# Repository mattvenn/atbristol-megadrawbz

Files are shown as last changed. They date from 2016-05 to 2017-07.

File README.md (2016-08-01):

# @bristol energy drawing robot

## updates

* [youtube playlist](https://www.youtube.com/playlist?list=PLmcDgdDpcaPiOdnMplbk7o1K5Kpvp_UAL)
* [photos](https://goo.gl/photos/KGhmjEyrZScbemvW7)

## details

### hardware

* [Beagle bone breakout board](hardware/bbbbbb_pcb/)
* [Pen holder](hardware/gondola_pcb/)
* [notes on stepper choice](tests/stepper-choice)

### machinekit/linuxcnc configuration

* Robot is controlled with machinekit running on a beaglebone black.
* Pen holder is controlled via Xbee radio and uses a [custom component] that runs in its own realtime thread.

* [configuration](https://github.com/mattvenn/machinekit-bipod)

### firmware

* [pen holder firmware](firmware/gondola/)

### tests

* [prototypes, tests, proof of concepts](tests)

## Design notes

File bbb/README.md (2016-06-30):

# Install

got latest image from
http://elinux.org/Beagleboard:BeagleBoneBlack_Debian#BBW.2FBBB_.28All_Revs.29_Machinekit

then flashed to sd card like
xzcat bone-debian-7.10-machinekit-armhf-2016-04-10-4gb.img.xz | sudo dd of=/dev/sdb

put into bbb and rebooted
username and password is machinekit

used linuxcnc to choose the CRAMPS config and that starts

install machinekit-dev to compile new hals

# Timings

## probotix example - cometnp_metric.ini
xstep is p9.31 11.2khz

default and max velocity for x axis increased to 1000
xstep is p9.31 43khz, nice and even

tested changing pin from 142 to 931 and worked the same

copied cramps settings and got speed of 95khz, less even

## cramps example - cramps.hal

xstep is p8.13 60khz

# Bipod setup

comp --install wanted a posix directory. Made and then copied over. Warning
about sqrt.

Can't start linuxcnc, got a permission error similar to stuarts.

to do with missing vtable in bipodkins. Clues from
https://groups.google.com/forum/#!searchin/machinekit/vtable$20kinematics/machinekit/qNgl9Eb5cbA/jJzNCTshsm0J

took code from
https://github.com/machinekit/machinekit/pull/560/commits/9b60f6636091e8badb550a7804e23cf311424cd2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

kins needs to be specified with motmod or will default to trivkins.

joint following errors were fixed (I think) by adding a maximum_acceleration in
the `[traj]` section.

# Serial setup

    # doesn't play well with the setup.sh that machinekit config uses
    echo BB-UART1 > /sys/devices/bone_capemgr.*/slots
    dmesg | grep tty

check connected xbee

    miniterm.py /dev/ttyO1 57600
    +++

replies with `OK`.

## path

add this to ~/.bashrc:

    PATH=$PATH:/home/machinekit/machinekit/configs/machinekit-bipod

not needed as can do loadusr ./xbee.py
loadusr needs -W parameter to wait till it initialises, probably why it was
occasionally failing on pc.

# startup issues

    Machine configuration directory is
    '/home/machinekit/machinekit/configs/machinekit-bipod'
    Machine configuration file is 'bipod.ini'
    Starting Machinekit...
    io started
    emc/iotask/ioControl.cc 752: can't load tool table.
    halcmd loadusr io started
    Loading cape-universal overlay to /sys/devices/bone_capemgr.9/slots
    X11 connection rejected because of wrong authentication.
    PRU control files not found in /sys/class/uio/uio0
    bipod.hal:10: program './setup.sh' failed, returned 1
    Shutting down and cleaning up Machinekit...

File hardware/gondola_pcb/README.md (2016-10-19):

# gondola PCB

## mods made

* connect xbee rx & tx to atmel rx & tx (no software serial) - solder wires to xbee header and connected a header that plugs into the programming header
* [lipo charger](http://dlnmh9ip6v2uc.cloudfront.net/datasheets/Prototyping/TP4056.pdf) soldered to the back, connected pin 7 to charge pin on pcb

## fixes required for next version

* lipo charger on board
* reset button
* reset xbee from atmega
* remote firmware update - arduino needs to reset itself 
* lipo socket that fits
* crystal footprint, no load caps required!
* lower frequency crtstal, mega328 is only guaranteed to 10mhz on 3.3v

## xbee firmware update

* has to be hw. tried sw and didn't work. used a 2n3904 to invert the signal and pull reset low
* haven't tried with xbee yet.
* wide timing window : 900ms before or after avrdude is run

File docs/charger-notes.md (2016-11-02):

# Tue Oct 18 14:46:19 CEST 2016

old charger (tp4506) and new (mcp73831) both can get stuck if the battery gets too low.
seems to be because xbee is drawing too much current so battery doesn't see enough

with xbee connected charge current is 0ma
with xbee disconnected is 10ma

current drawn on circuit is 50ma without xbee, 100 with. Why so high without?
should be about 6ma.

could be worth looking at xbee sleep modes before hacking on power control
(need to do ATSM1 to enable pin)

could also put a mosfet on the charger board that will not connect main board until vbatt > thresh

thoughts:
* 500ma maybe too high a charge current
* make sure charge sense pin can't do damage to atmega

charge sense pin on broken pcb seems shorted to ground, need to check the
old charger pcb

# Wed Oct 19 15:21:23 CEST 2016

why did charge pin get damaged?

* input higher than supply voltage?

charge sense pin was (I think - should have taken a photo before disconnecting)
connected to other side of diode. This voltage is then the diode drop over the
diode subtracted from the supply (which I think I cranked to about 5.5v - again
don't have a record). So about 3.6->4v. And the supply of the chip was 3.3v so
that was probably it.

The same will happen with the mcp73831 as the stat pin goes high when charge is
finished, the high level is vdd-1 so 4v.

# Wed Oct 19 17:39:25 CEST 2016

* questions - why current draw so high?
* why won't battery charger to higher than 3.8?

battery doc is 
http://es.rs-online.com/webdocs/141b/0900766b8141bf6b.pdf

# Thu Oct 27 18:51:30 CEST 2016

* discharged at 400ma till cutoff
* testing with 171ma current limit with battery fully discharged (v drops to
 3.7v)

start, gondola comes on, but has problems with comms:

inekit@devel:~/bipod$ halcmd  show | grep xbee
    94  User          0 xbee                                      18964 ready, u1:0 u2:0
    94        u32   OUT    0x00001AA8  xbee.cksum-err 0
    94        float OUT          0.26  xbee.gond_batt                   0.000010 0
    94        u32   OUT    0x0000AA6B  xbee.gond_err_count 0
    94        u32   OUT    0x00000000  xbee.gond_flags 0
    94        u32   OUT    0x00000000  xbee.gond_rx_count 0
    94        u32   OUT    0x00000000  xbee.gond_touch 0
    94        float IN              8  xbee.pos                         0.000010 0 <== zpos
    94        u32   OUT    0x0001280B  xbee.rx-err 0
    94        bit   IN           TRUE  xbee.servo_enable 0 ==> xbee.pos
    94        float RW             20  xbee.scale

comms problem fixed with start byte.

Also changed to 300mA charge current

# Wed Nov  2 09:22:05 CET 2016

[low-power-test.sh](low-power-test.sh) used to test what happens with constant
discharge and recharge at the cutoff point. 
[Results show no problems](low-power.log)

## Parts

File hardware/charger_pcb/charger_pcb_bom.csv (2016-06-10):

Qty | Value | Device | Package | Parts | Description | RS code | Link
2 |  | AK500/2 | AK500/2 | X1, X2 | CONNECTOR | 2204260 | http://uk.rs-online.com/web/p/pcb-terminal-blocks/2204260/
1 |  | LEDCHIP-LED0805 | CHIP-LED0805 | POWER | LED | 8886057 | http://uk.rs-online.com/web/p/visible-leds/9154768/
2 |  | N-MOSFET-SO8S | SO-08 | Q1, Q2 | N-Channel MOSFET | 915-4960 | http://uk.rs-online.com/web/p/mosfet-transistors/9154960/
1 | 0.01uF | C-EUC0805 | C0805 | C2 | CAPACITOR, European symbol | 4614013 | http://uk.rs-online.com/web/p/ceramic-multilayer-capacitors/4614013/
1 | 0.01uf | C-EUC0805 | C0805 | C1 | CAPACITOR, European symbol | 4614013 | http://uk.rs-online.com/web/p/ceramic-multilayer-capacitors/4614013/
1 | 0.3uF | C-EUC0805 | C0805 | C3 | CAPACITOR, European symbol | 6983421 | http://uk.rs-online.com/web/p/ceramic-multilayer-capacitors/6983421/
2 | 100R | R-EU_R0805 | R0805 | R1, R2 | RESISTOR, European symbol | 6790807 | http://uk.rs-online.com/web/p/surface-mount-fixed-resistors/6790807/
1 | 16VZ | ZENER-DIODESOD80C | SOD80C | D2 | Z-Diode | 7598775 | http://uk.rs-online.com/web/p/zener-diodes/7598775/
1 | 16vZ | ZENER-DIODESOD80C | SOD80C | D1 | Z-Diode | 7598775 | http://uk.rs-online.com/web/p/zener-diodes/7598775/
1 | 220R | R-EU_R0805 | R0805 | R3 | RESISTOR, European symbol | 2230332 | http://uk.rs-online.com/web/p/surface-mount-fixed-resistors/2230332/
2 | 40V2A | MBRA340T3 | SMA | D3, D4 | Surface Mount Schottky Power Rectifier | 708-2337 | http://uk.rs-online.com/web/p/rectifier-schottky-diodes/7082337/
2 | 68uH | L-EUL5650M | L5650M | L1, L2 | INDUCTOR, European symbol | 6924930 | http://uk.rs-online.com/web/p/wire-wound-surface-mount-inductors/6924930/

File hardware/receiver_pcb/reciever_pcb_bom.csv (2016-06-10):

Part | Value | Device | Package | Description | RS code | Link
C1 | 4.7nF | C-EUC0805 | C0805 | CAPACITOR, European symbol | 4646717 | http://uk.rs-online.com/web/p/ceramic-multilayer-capacitors/4646717/
C2 | 4.7nF | C-EUC0805 | C0805 | CAPACITOR, European symbol | 4646717 | http://uk.rs-online.com/web/p/ceramic-multilayer-capacitors/4646717/
C3 | 22nF | C-EUC0805 | C0805 | CAPACITOR, European symbol | 4646701 | http://uk.rs-online.com/web/p/ceramic-multilayer-capacitors/4646701/
C4 | 1.8nF | C-EUC0805 | C0805 | CAPACITOR, European symbol | 7236225 | http://uk.rs-online.com/web/p/ceramic-multilayer-capacitors/7236225/ | Low ESR
C5 | 10uF | C-EUC0805 | C0805 | CAPACITOR, European symbol | 9159280 | http://uk.rs-online.com/web/p/ceramic-multilayer-capacitors/9159280/ | Low ESR
C6 | 2.2uF | C-EUC0805 | C0805 | CAPACITOR, European symbol | 8919794 | http://uk.rs-online.com/web/p/ceramic-multilayer-capacitors/8919794/
C7 | 10nF | C-EUC0805 | C0805 | CAPACITOR, European symbol | 4614013 | http://uk.rs-online.com/web/p/ceramic-multilayer-capacitors/4614013/
D1 | DFLS240L | DFLS240L | POWERDI123 |  | 7082337 | http://uk.rs-online.com/web/p/rectifier-schottky-diodes/7082337/ | Ordered 10 on charger, 10 on reciever
D2 | DFLS240L | DFLS240L | POWERDI123 |  | 7082337 | http://uk.rs-online.com/web/p/rectifier-schottky-diodes/7082337/
D3 | DFLS240L | DFLS240L | POWERDI123 |  | 7082337 | http://uk.rs-online.com/web/p/rectifier-schottky-diodes/7082337/
D4 | 39VZ | DFLZ39 | POWERDI123 |  | 822-2497 | http://uk.rs-online.com/web/p/zener-diodes/8222497/
L1 | 15uH | L-EUL1812 | L1812 | Toko coil | 7521327 | http://uk.rs-online.com/web/p/wire-wound-surface-mount-inductors/7521327/ | out of stock, using this: http://uk.rs-online.com/web/p/wire-wound-surface-mount-inductors/0573858/
LED1 |  | LEDCHIP-LED0805 | CHIP-LED0805 | LED |  | http://uk.rs-online.com/web/p/visible-leds/9154768/ | ordered on charger
LED2 |  | LEDCHIP-LED0805 | CHIP-LED0805 | LED |  | http://uk.rs-online.com/web/p/visible-leds/9154768/
R1 | 3.01K | R-EU_R0805 | R0805 | RESISTOR, European symbol | 6791349 | http://uk.rs-online.com/web/p/surface-mount-fixed-resistors/6791349/
R2 | 10K | R-EU_R0805 | R0805 | RESISTOR, European symbol | 2230562 | http://uk.rs-online.com/web/p/surface-mount-fixed-resistors/2230562/
R3 | 22k | Pot |  | Charge limiting pot | 5219754 | http://uk.rs-online.com/web/p/trimmer-resistors/5219754/
R4 | 470 | R-EU_R0805 | R0805 | RESISTOR, European symbol | 2230376 | http://uk.rs-online.com/web/p/surface-mount-fixed-resistors/2230376/
R5 | 470 | R-EU_R0805 | R0805 | RESISTOR, European symbol | 2230376 | http://uk.rs-online.com/web/p/surface-mount-fixed-resistors/2230376/
U$1 | LT4120 | LT4120 | QFN16 |  |  |  | Matt has them, for free!
X1 |  | AK500/2 | AK500/2 | CONNECTOR |  | http://uk.rs-online.com/web/p/pcb-terminal-blocks/2204260/ | ordered on charger
X2 |  | AK500/2 | AK500/2 | CONNECTOR |  | http://uk.rs-online.com/web/p/pcb-terminal-blocks/2204260/ | ordered on charger
X3 |  | KK-156-3 | KK-156-3 | KK 156 HEADER |  |  | Matt has them, and also a crimper
X4 |  | AK500/2 | AK500/2 | CONNECTOR | 5151383 | http://uk.rs-online.com/web/p/pcb-headers/5151383/ | Jst battery connector
 | 2000mA/h |  |  | Lipo | 7916460 | http://uk.rs-online.com/web/p/lithium-rechargeable-battery-packs/7916460/

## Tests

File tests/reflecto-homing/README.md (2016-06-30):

# Testing reflective homing

This method of homing is interesting to explore because it means our home point can be in the middle of the robot's range rather than at the edges. The edges are harder to get to because if the motors aren't co-ordinated (like at power on) there can be too much tension in the strings.

It's also interesting because if we can sense the string on the spool we have a 1 bit absolute position sensor. This means even if this method can't provide precision homing, it will help move the motors to a safe starting place before a more traditional homing method is used.

Test shows the homing is accurate to within +- 0.15mm (on a 19mm spool). However, the results are susceptible to changes in ambient light. With a torch I can produce a 0.5mm error.

## Setup

[Video](https://www.youtube.com/watch?v=r71VegIOap8&feature=youtu.be)

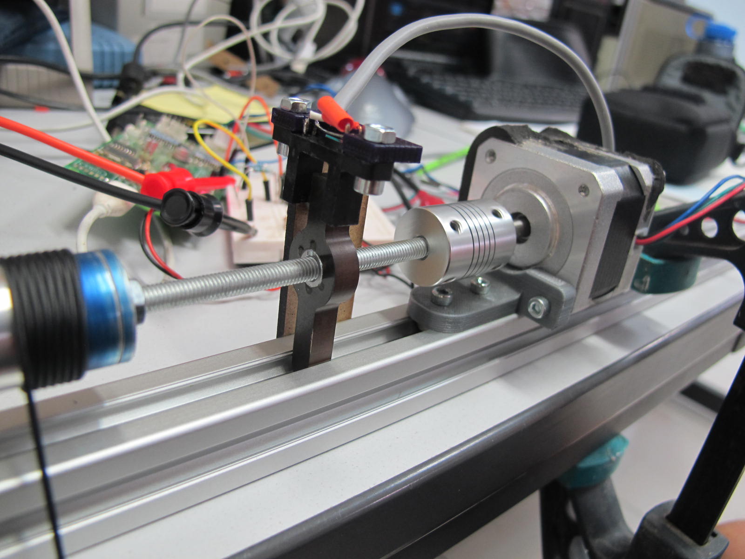
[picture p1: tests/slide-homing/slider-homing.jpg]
setup


* 1600 count encoder with thread wrapped twice
* 8 time microstepping
* 12v
* 0.2A
* 130g weight
* using [OPB608A](http://uk.rs-online.com/web/p/photoelectric-sensors/1944018/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)

## Results

* spool is black nylon with a 1mm thread, string is generic brown braid, about 0.8mm

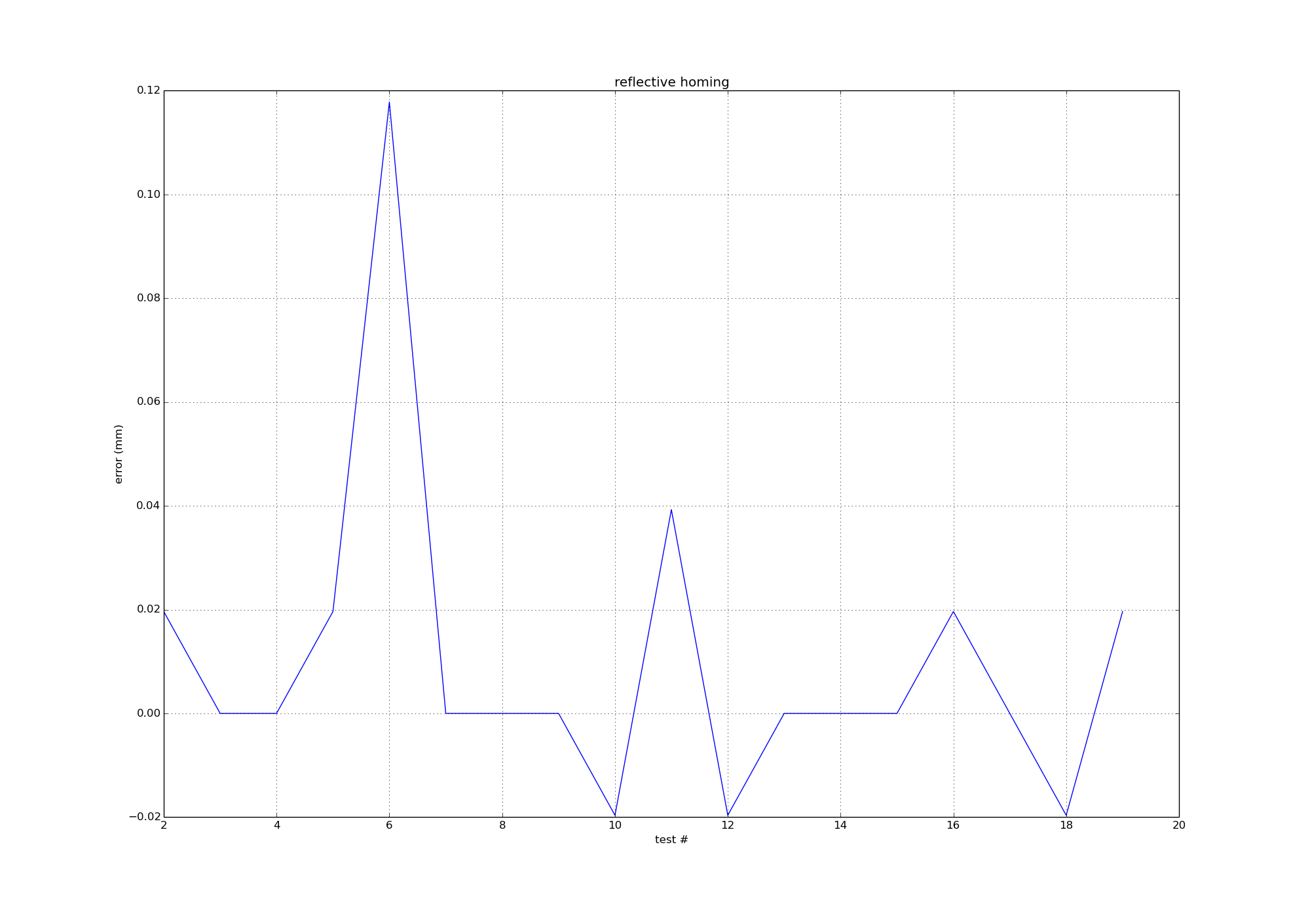
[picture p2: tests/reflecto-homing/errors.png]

[data](home_errors.pkl)

* black 1mm dyneema on aluminium spool, 10k R on opto collector

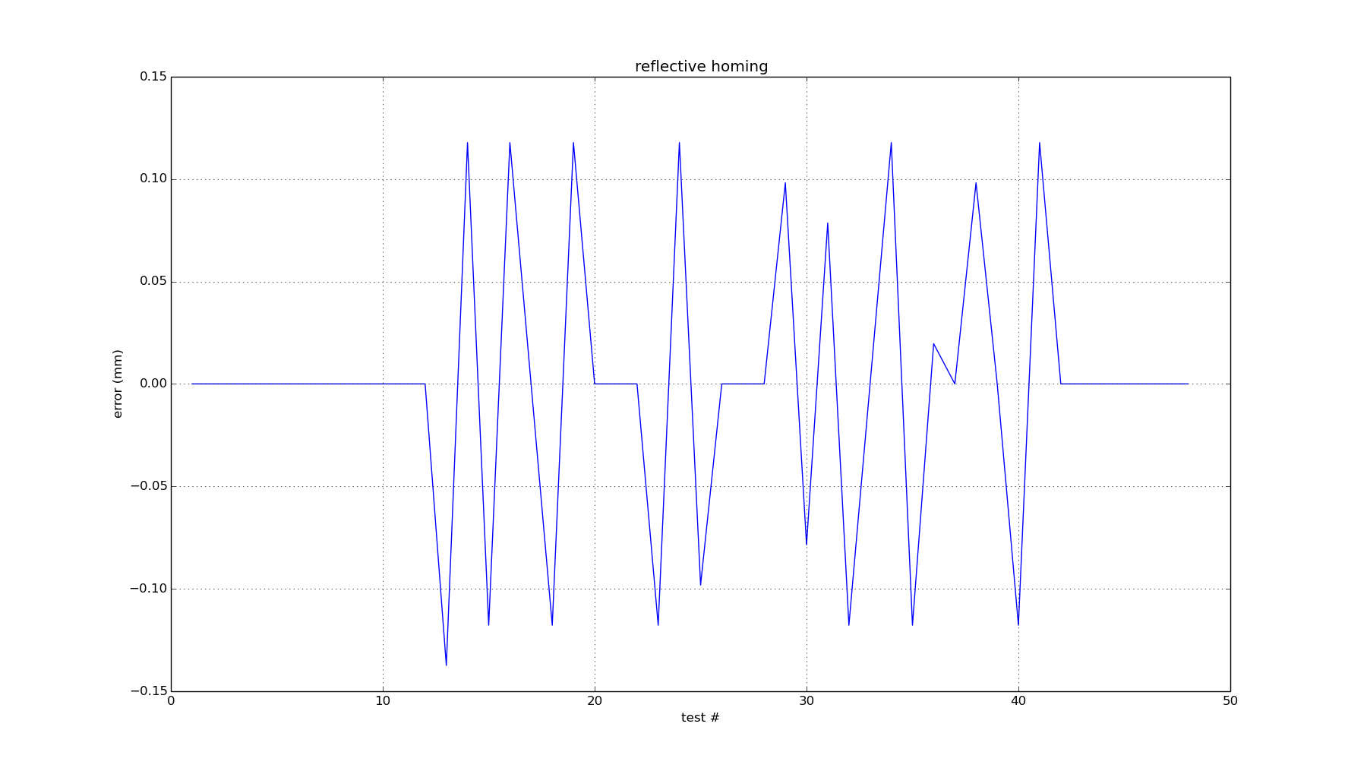
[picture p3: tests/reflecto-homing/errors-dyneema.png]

[data](home_errors-dyneema.pkl)

* black 1mm dyneema on aluminium spool, screwthread 1.3mm

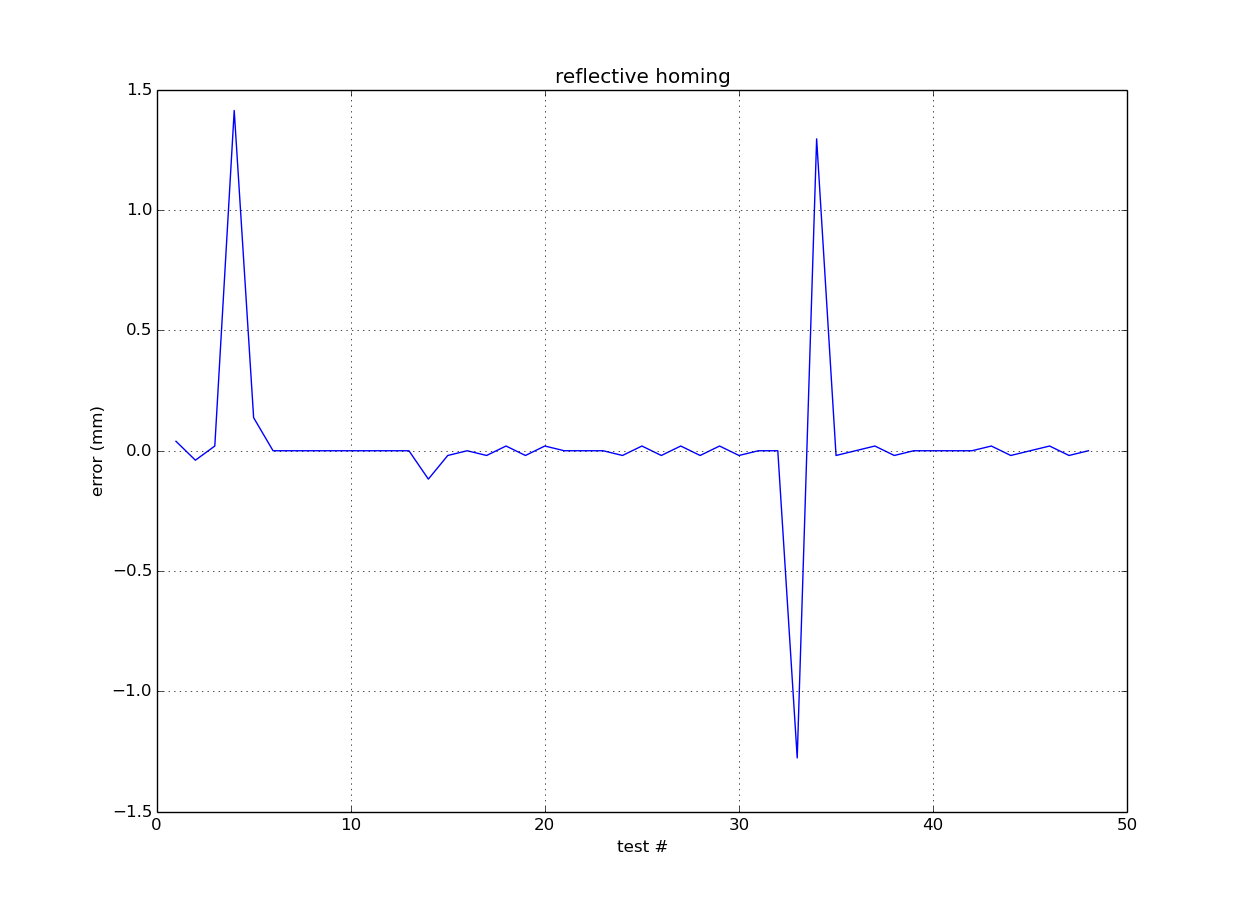
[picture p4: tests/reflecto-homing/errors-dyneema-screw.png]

[data](home_errors-dyneema-screwthread.pkl)

* 20uf cap on opto supply and 100nf on opto output, slowed home speed

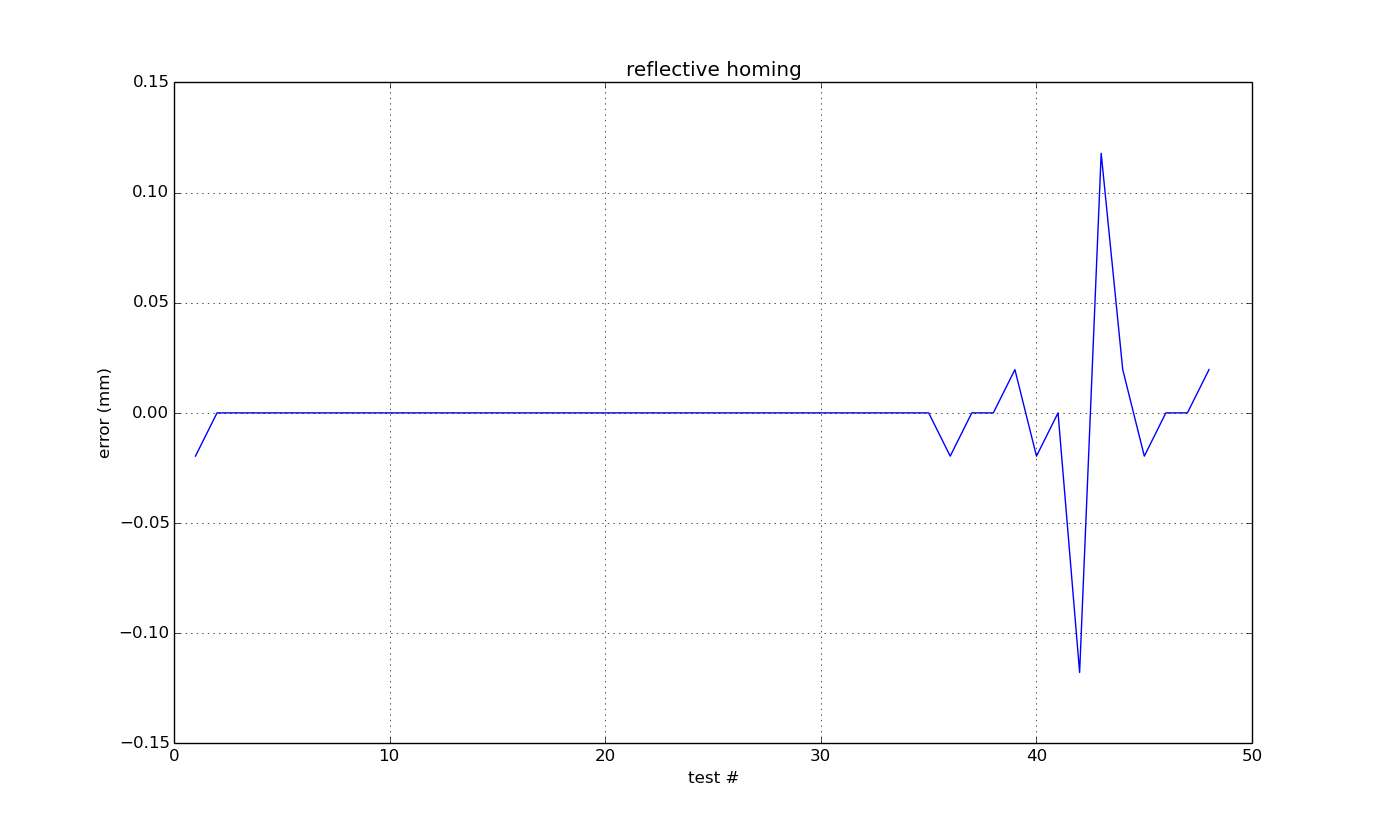
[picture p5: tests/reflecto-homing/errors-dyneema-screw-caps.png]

[data](home_errors-dyneema-screwthread-caps.pkl)

* same as last test but sensor rotated 90

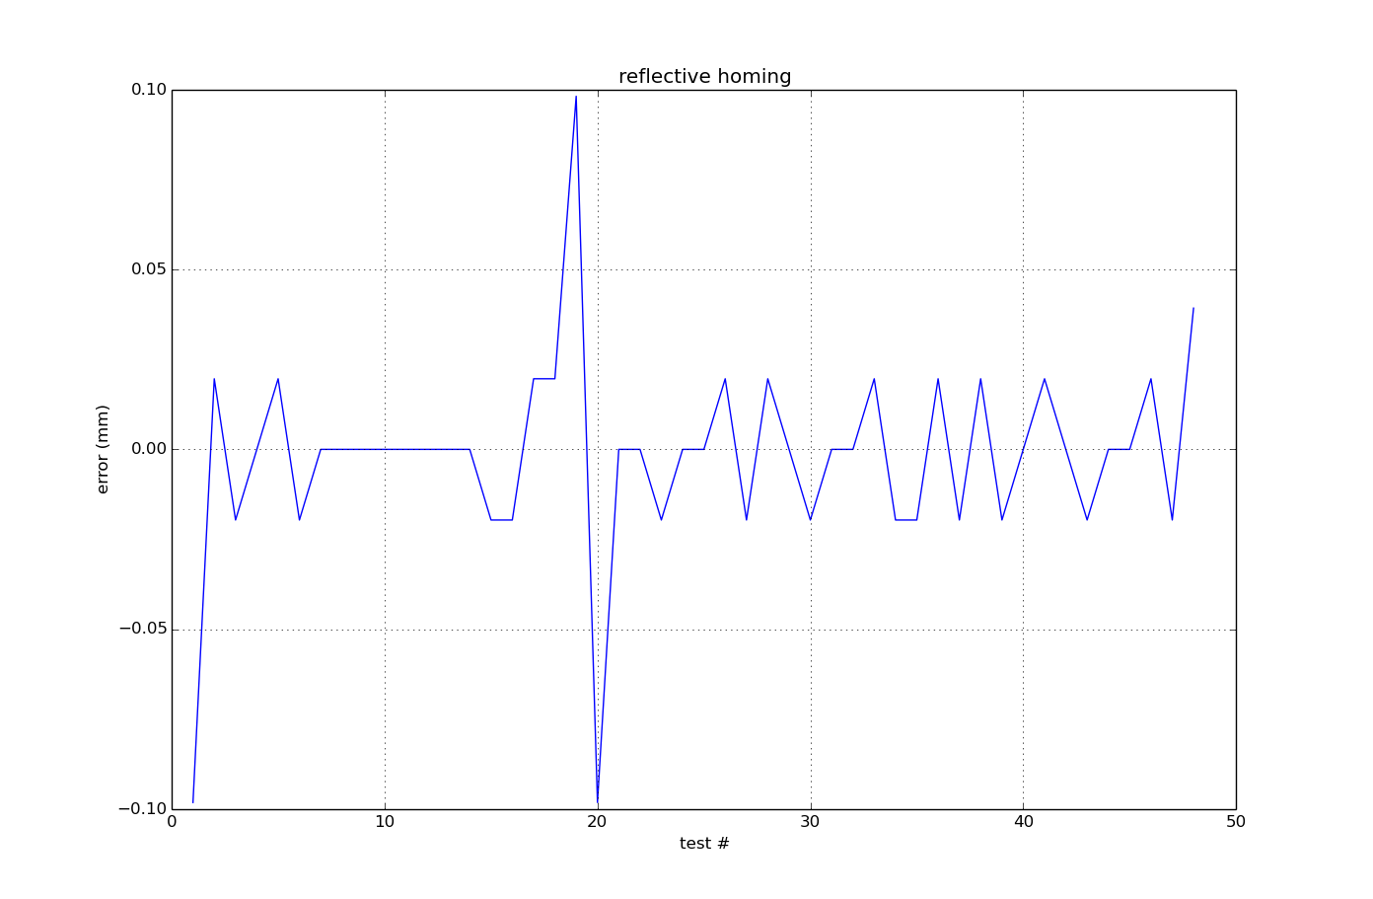
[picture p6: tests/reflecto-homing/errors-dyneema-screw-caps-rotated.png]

[data](home_errors-dyneema-screwthread-caps-rotated.pkl)

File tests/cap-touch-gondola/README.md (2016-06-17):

# capacitive touch on the gondola

If people lift the gondola the strings can unwind or get tangled

We're planning on using PTFE tube for the string to run through at the top corners, which will stop the lack of tension getting through to the spools.

However if the gondola is lifted if the spools are unwinding the string could get tangled up.

So this test is to see if the gondola can sense when it's touched, and send a signal to linuxcnc to pause the drawing.

We were worried that without a ground connection the capacitive touch method wouldn't work, but it seems to work fine.

# method

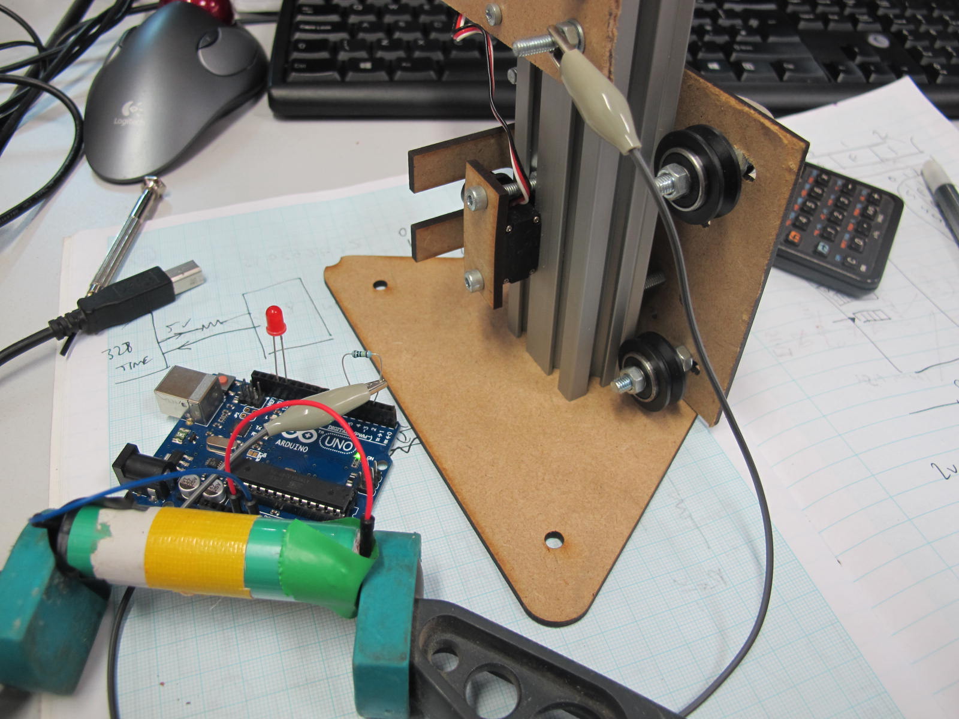
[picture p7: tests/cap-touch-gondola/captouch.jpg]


[video](https://www.youtube.com/watch?v=7M-Ta0E2XPM&feature=youtu.be)

a 1M resistor is connected between 2 pins. One of the pins is also connected to the aluminium of the gondola.

# test code

[cap.ino](cap.ino)

using this [capacitive touch library](https://github.com/PaulStoffregen/CapacitiveSensor)

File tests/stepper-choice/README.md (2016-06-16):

# Stepper choice

specs:

* 1Nm to provide resistance against tampering
* string on a 35mm spool to reduce wrapping (and therefore hyp error)
* hyp error <= 0.2mm over travel
* max spd >= 150mm/s
* res <= 0.2 mm/step

# chosen option:

* motor: http://uk.rs-online.com/web/p/stepper-motors/5350423/
* 1nm at 2.8A, 200 steps per rev
* 1 : 1.8 pulley ratio

[datasheet](http://docs-europe.electrocomponents.com/webdocs/07e2/0900766b807e2898.pdf)

We should be able to achieve 1nm with about half the rated current but if
necessary we can increase the current. We also have options to increase torque
by decreasing microstepping at the cost resolution.

At 2000hz step freq, we achieve 150mm/s and datasheet says torque is derated by
20%.

## option 1

http://uk.rs-online.com/web/p/stepper-motors/5350502/
400 steps/rev, 1.26nm, 2.8A

config: micro steps is 2, and motor is directly attached

20% overrated so can run at 2.2A
cost = £35

## option 2

http://uk.rs-online.com/web/p/stepper-motors/5350401/?origin=null|fp&cm_sp=featureproducts-_-FeaturedProductsContent-_-5350401

200 steps/rev
0.44Nm, 1.68A

config: micro steps is 2, motor is attached with 1:2 pulley

cost = £27 + pulleys & belts (£11 + £3)
total = £40

notes: slightly underrated

## option 3

http://uk.rs-online.com/web/p/stepper-motors/5350445/
1.89Nm 2.8A

directly attached with 4 x microstepping
cost = £41.20

notes: 2.8A is above the drivers can supply

# Driver

## drv8825

rds on at 85C = 0.32R
page 23 data sheet:

    Ptot = 4*rdson*(iout)^2
    = 6W dissipation

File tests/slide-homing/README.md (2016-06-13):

# Testing sliding homing

The [reflective homing
method](https://github.com/mattvenn/atbristol-megadrawbz/tree/master/tests/reflecto-homing) had some good benefits, but suffered from unreliability
with changing light conditions. In particular we wanted to keep the absolute
positioning to aid with homing. Ideally we want the method to be good enough for
homing (better than 0.3mm error).

For this test we coupled the spool with a screwthread and used the thread to
drive a slider that interrupted the photo interrupter.

Results show better than opto homing (0.12mm max error on a 19mm spool), and
much more reliable. With a bit more tuning we should get even lower errors, but
our calculations show that 0.3mm error is acceptable.

## Setup

setup

[Video here](https://www.youtube.com/watch?v=r71VegIOap8&feature=youtu.be)

* 8 time microstepping
* 12v
* 0.2A
* m6 threaded bar, rexroth extrusion for rail
* direct drive stepper
* 10k R on opto collector [Optek OPB815L](http://uk.rs-online.com/web/p/slotted-optical-switches/1944024/)
* 35mm diameter spool

## Results

All plots show errors in mm calculated for a 35mm diameter spool.

* 2000 steps and with a short backoff. 

[data](error-2000step.pkl) 
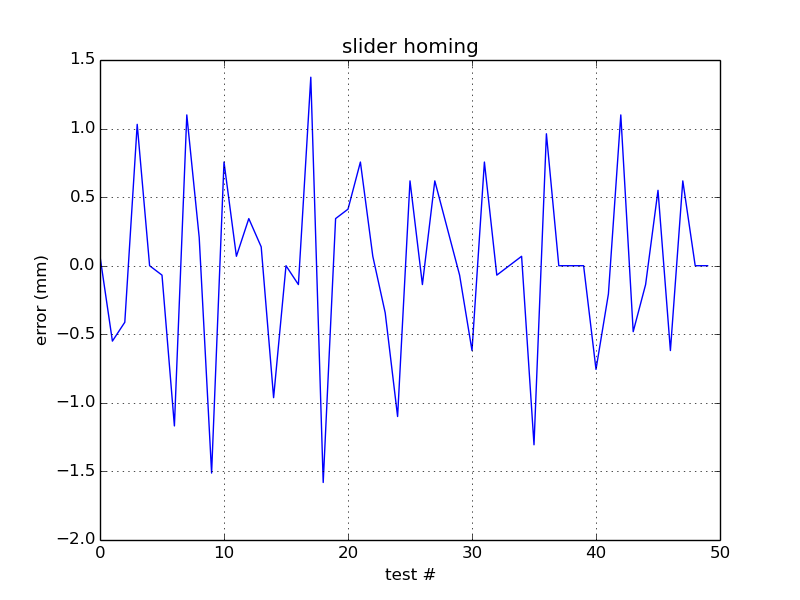
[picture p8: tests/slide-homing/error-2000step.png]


* tufnol slider, pressfit nut, 4000 step

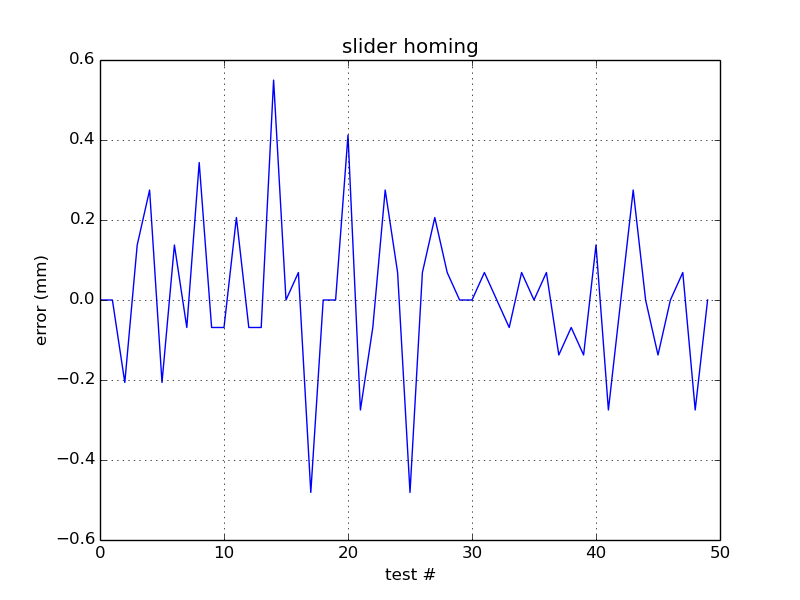
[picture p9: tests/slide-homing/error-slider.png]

[data](error-slider.pkl)

The slider was doing some wobbling, tried with a spring but made it worse.

* 3d printed slider with 2 press fit nuts

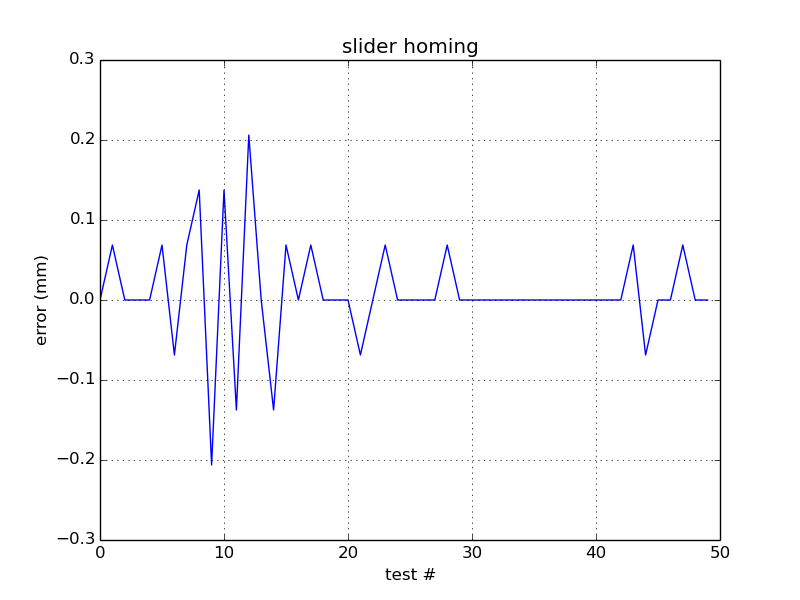
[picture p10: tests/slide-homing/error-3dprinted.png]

[data](error-3dprinted.pkl)

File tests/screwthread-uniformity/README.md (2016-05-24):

# Testing screw thread uniformity

setup



* standard M10 threaded bar mounted to NEMA17 200 steps per rev stepper
* 8 time microstepping
* 12v
* 0.2A
* 130g weight

[Test program](test.py) sends steps for 10 revolutions, recording encoder position at each 20 step interval.

[firmware](screwthread-uniformity.ino) is running on Arduino.

# Results

Graphs generated by [plot.py](plot.py)

* Green line is 1 to 1 stepper to encoder (perfect linearity)
* Blue line is measured stepper vs encoder

## 300 mm

300mm between enc and step

Graph shows excellent linearity between steps and string length

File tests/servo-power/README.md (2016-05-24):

# Battery servo test

## mini servo measurements

* using 10R resister to measure current on scope. 
* Movement from 0 to 100 degrees takes 300ms
* Multimeter shows peak 180mA, avg seems about 30mA
* Integrated curve with scope and got 90mvS, divide by 10R to get 9mAS

* movements each use 9mAS = 0.0025mAH. So to consume 500mAH is 200k moves
* 2k moves use 5mAH

To do a proper test need to move servo more frequently and use a much lower capacity battery.

## Test spec

arduino powered by laptop, servo powered by battery
battery is Panasonic NCR 18650 A Li-Ion 3100mAh 3.7V - [discharge curve](http://2.bp.blogspot.com/-QMeGi0AFhtQ/T2ztWwjDEEI/AAAAAAAADOk/ZcpiqvsJT-g/s1600/Panasonic+3100mAh.jpg)
1 movement every second
4.20V battery at Thu May 19 11:50:19 CEST 2016

2k movements in 2k s = 33min. Test stopped at 12:23. Battery voltage = 4.17V
Additional 2k moves goes to 4.15V
predicted 4v

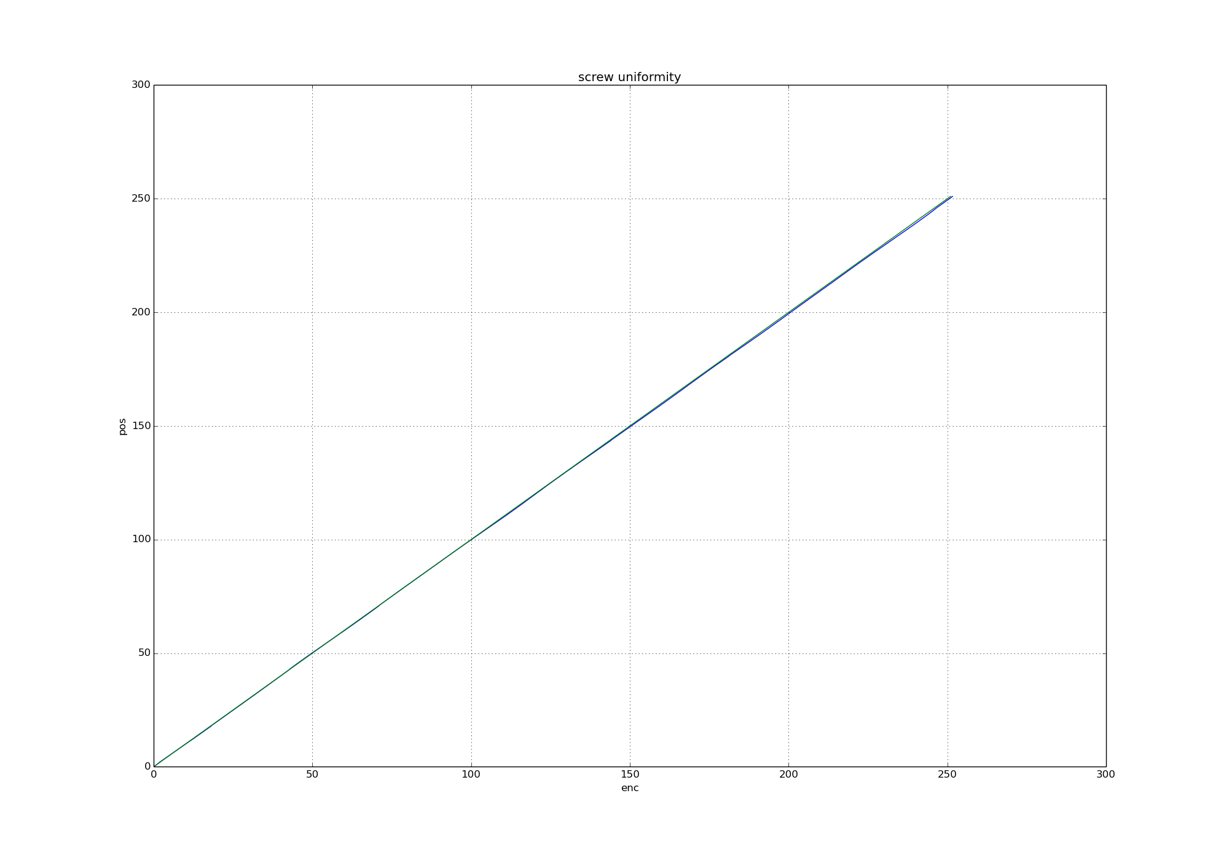
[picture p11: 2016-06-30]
tests/screwthread-uniformity/figure_30-dyneema.png

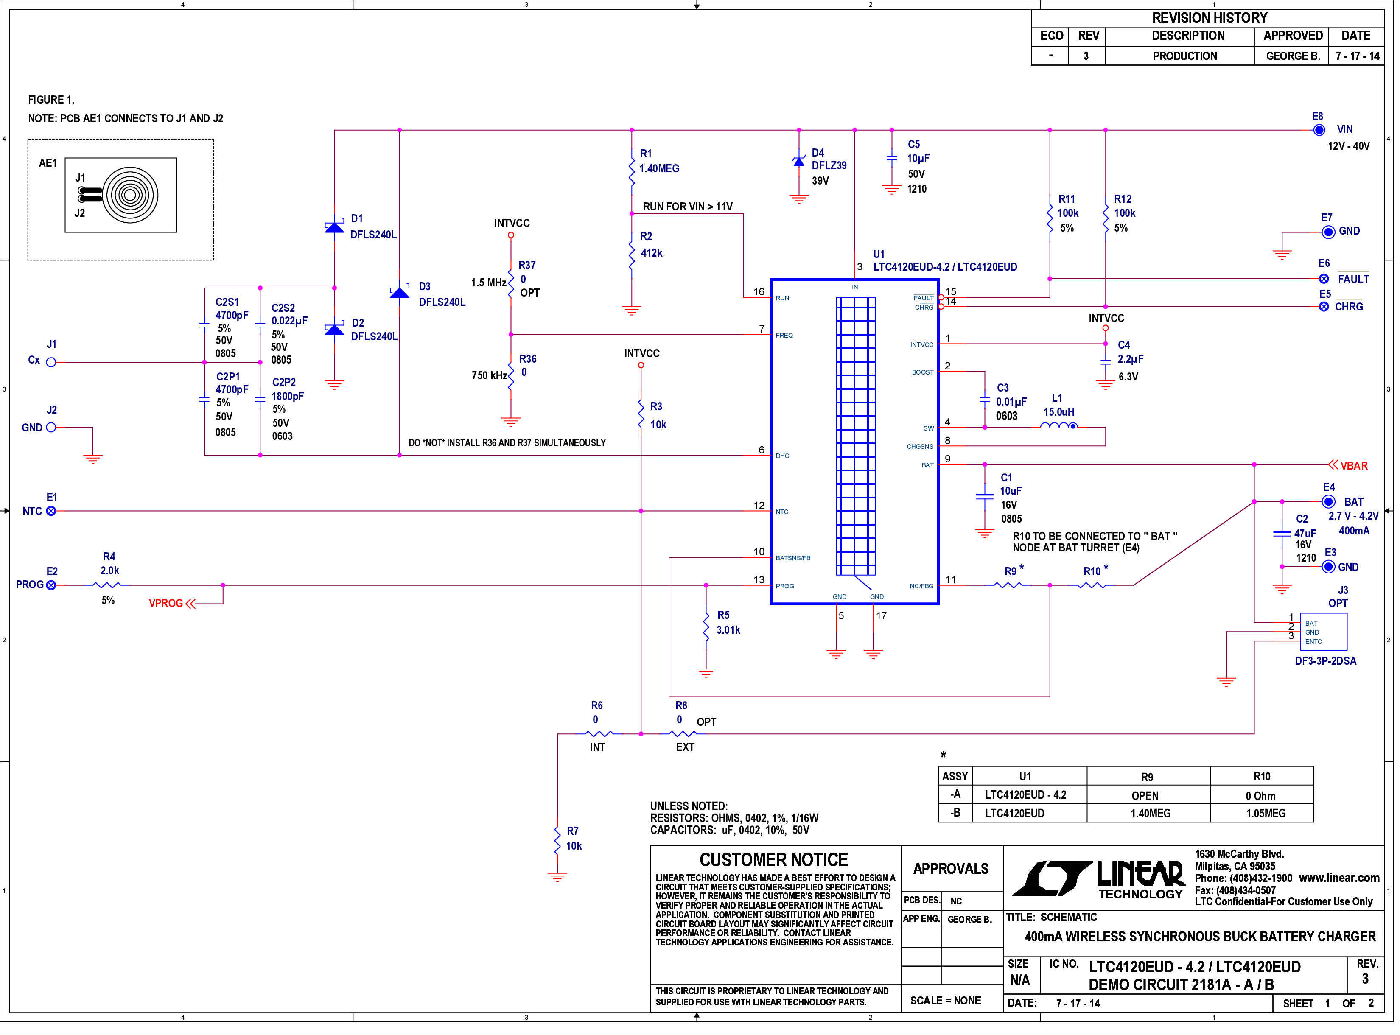
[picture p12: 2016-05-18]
hardware/receiver_pcb/linear test pcb schematic.png

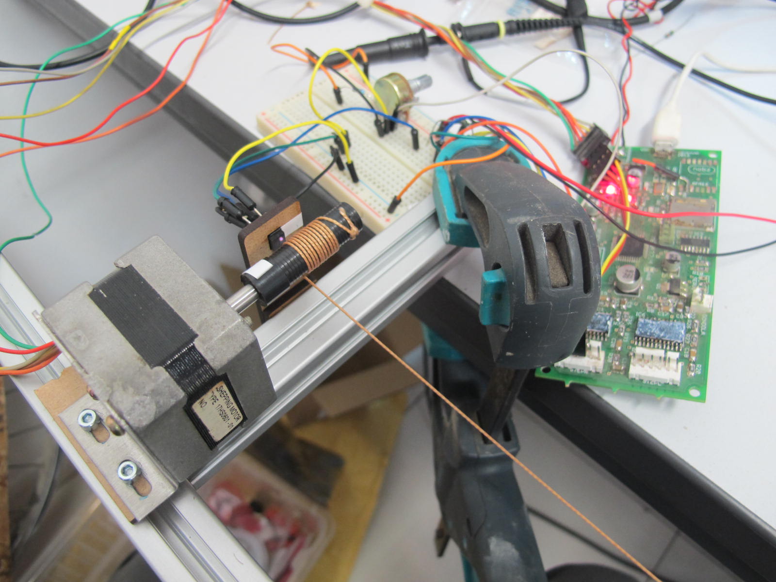
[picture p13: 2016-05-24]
tests/reflecto-homing/ref_homing.jpg

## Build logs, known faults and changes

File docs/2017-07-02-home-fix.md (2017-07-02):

Reset home position

* measured from pulleys and changed in bipod.ini, was 25mm diff on both sides
* was bottoming out at bottom of the circle, so reduced top margin
* changed top margin from 600 to 500 in the cursivedata db on mattvenn.net
* roll fitted wrong way round, so ratchet isn't working

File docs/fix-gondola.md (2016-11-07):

# Gondola fix

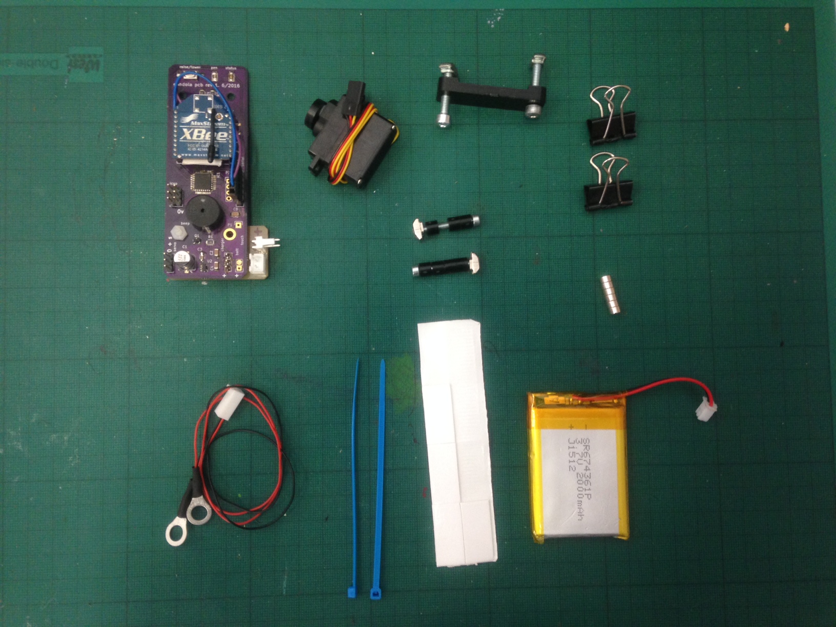
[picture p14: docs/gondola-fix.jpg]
gondola fix kit


## tools required

* 2.5mm hex
* 3mm hex
* small cross head screwdriver
* 8mm spanner
* ladder

## work required

### install servo

* cam angle will need adjusting before fitting
* use cable tie to shorten excess cable

### install battery

* use sticky pads to hold in place, check PCB position first

### install pcb

* use 1 spacer above and 2 below at one end, and 1 above and 3 below for the other
* plug in battery (polarised plug)
* plug in servo (non polarised plug so note polarity on pcb - black is 0v)

### install charger cable

* check polarity of charger hangers before attaching wires to the bolts
* plug in charger cable (polarised plug)

### adjust pen set tool

* after servo change will need to adjust pen test

### improve charger connection

* clean conductive grease
* try out magnets, hold in place with clips
* put conductive grease on charging hangers

# String untangle

## tools required

* 5mm hex key for bolts

## work required

* untangle string
* check homing works correctly

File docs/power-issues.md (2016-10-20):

# Thu Oct 20 11:45:22 CEST 2016

trying to track down spurious power downs:

tried with a brand new beagleboard and this happened within 5 mins!

on terminal:

    Broadcast message from root@devel (Sun Apr 10 20:26:04 2016):

    Power button pressed 
    The system is going down for system halt NOW!

http://bugs.elinux.org/issues/85

trying this:
http://unix.stackexchange.com/questions/114535/system-is-going-down-for-reboot-now

and got this:

    root       575     1  0 11:41 ?        00:00:00 /usr/sbin/acpid
    root     11680   575  0 13:10 ?        00:00:00  \_ /bin/sh -c
    /etc/acpi/powerbtn-acpi-support.sh
    root     11681 11680  0 13:10 ?        00:00:00      \_ /bin/sh
    /etc/acpi/powerbtn-acpi-support.sh
    root     11721 11681  0 13:10 ?        00:00:00          \_ /bin/bash
    /sbin/shutdown -h -P now Power button pressed
    root     11723 11721  0 13:10 ?        00:00:00              \_ ps -ef --forest

So it's a bug in the hardware or software, but easy to fix.

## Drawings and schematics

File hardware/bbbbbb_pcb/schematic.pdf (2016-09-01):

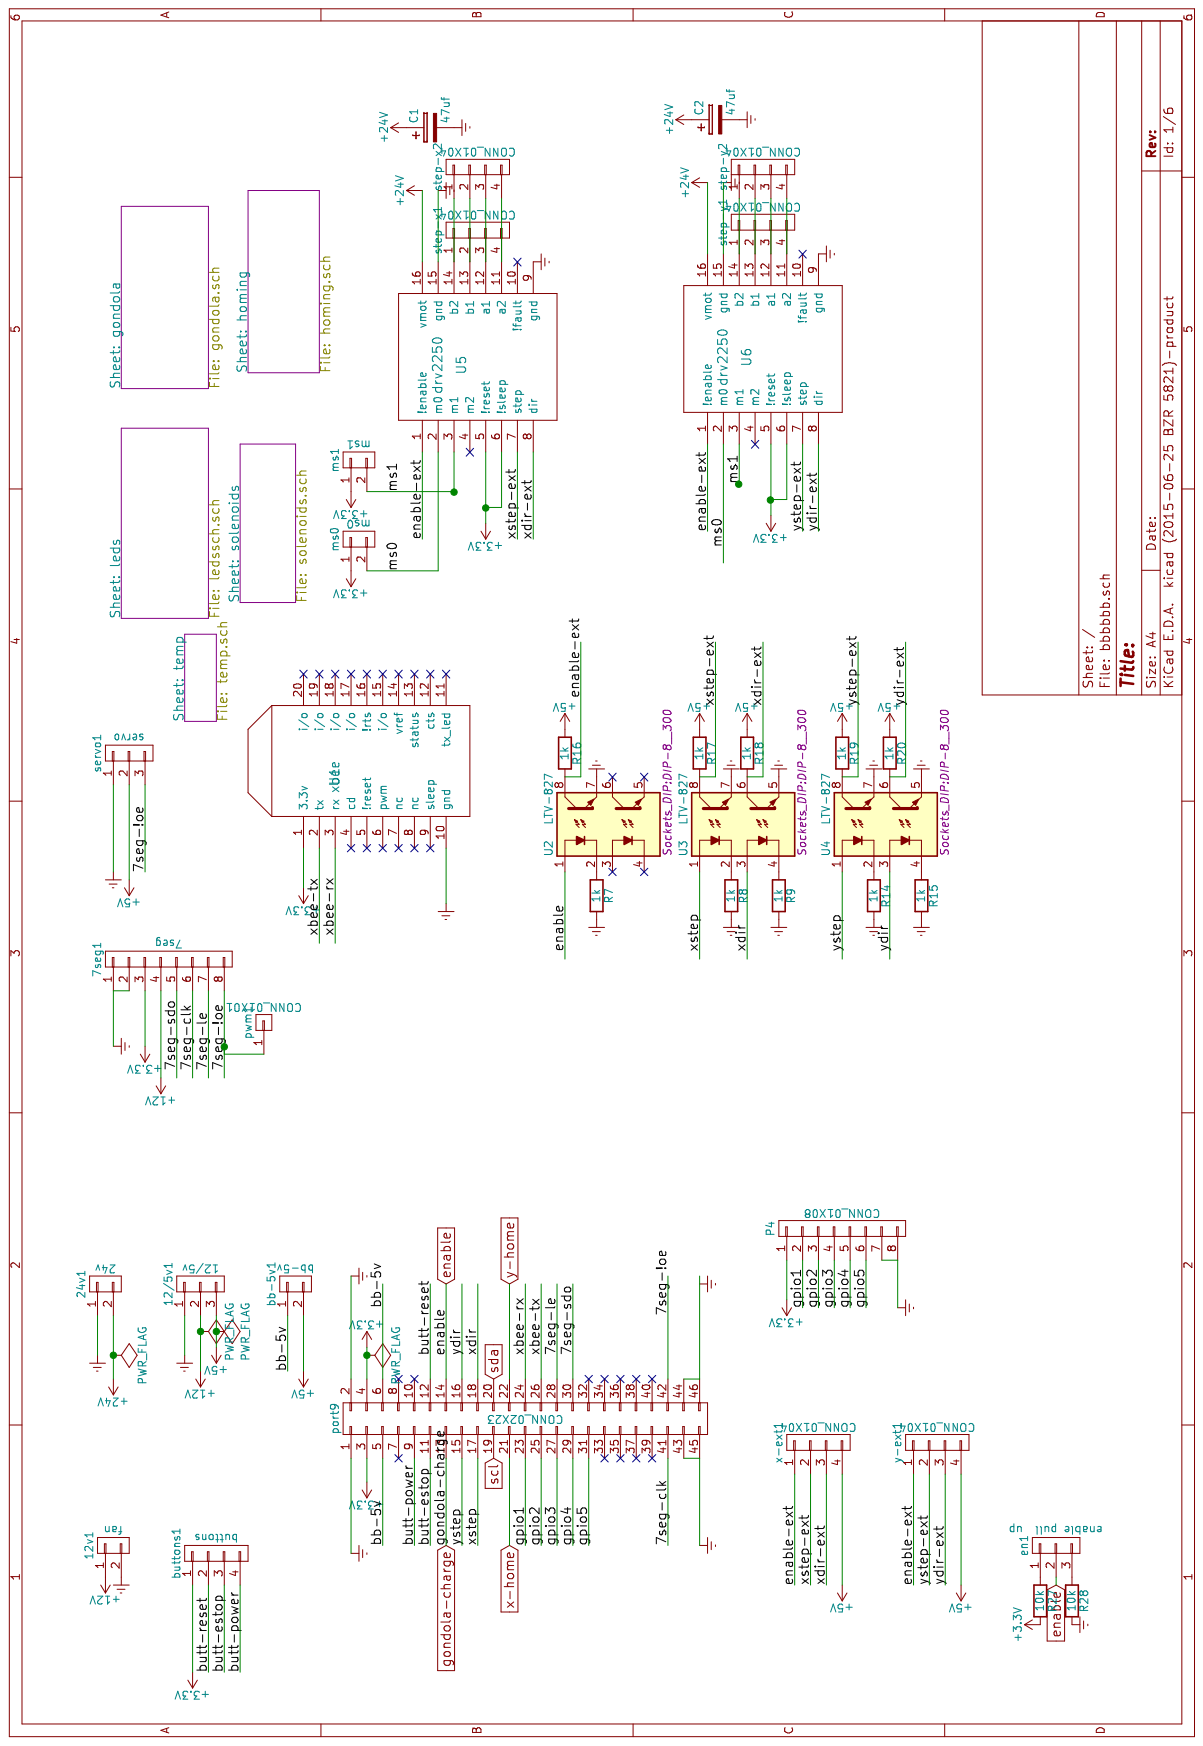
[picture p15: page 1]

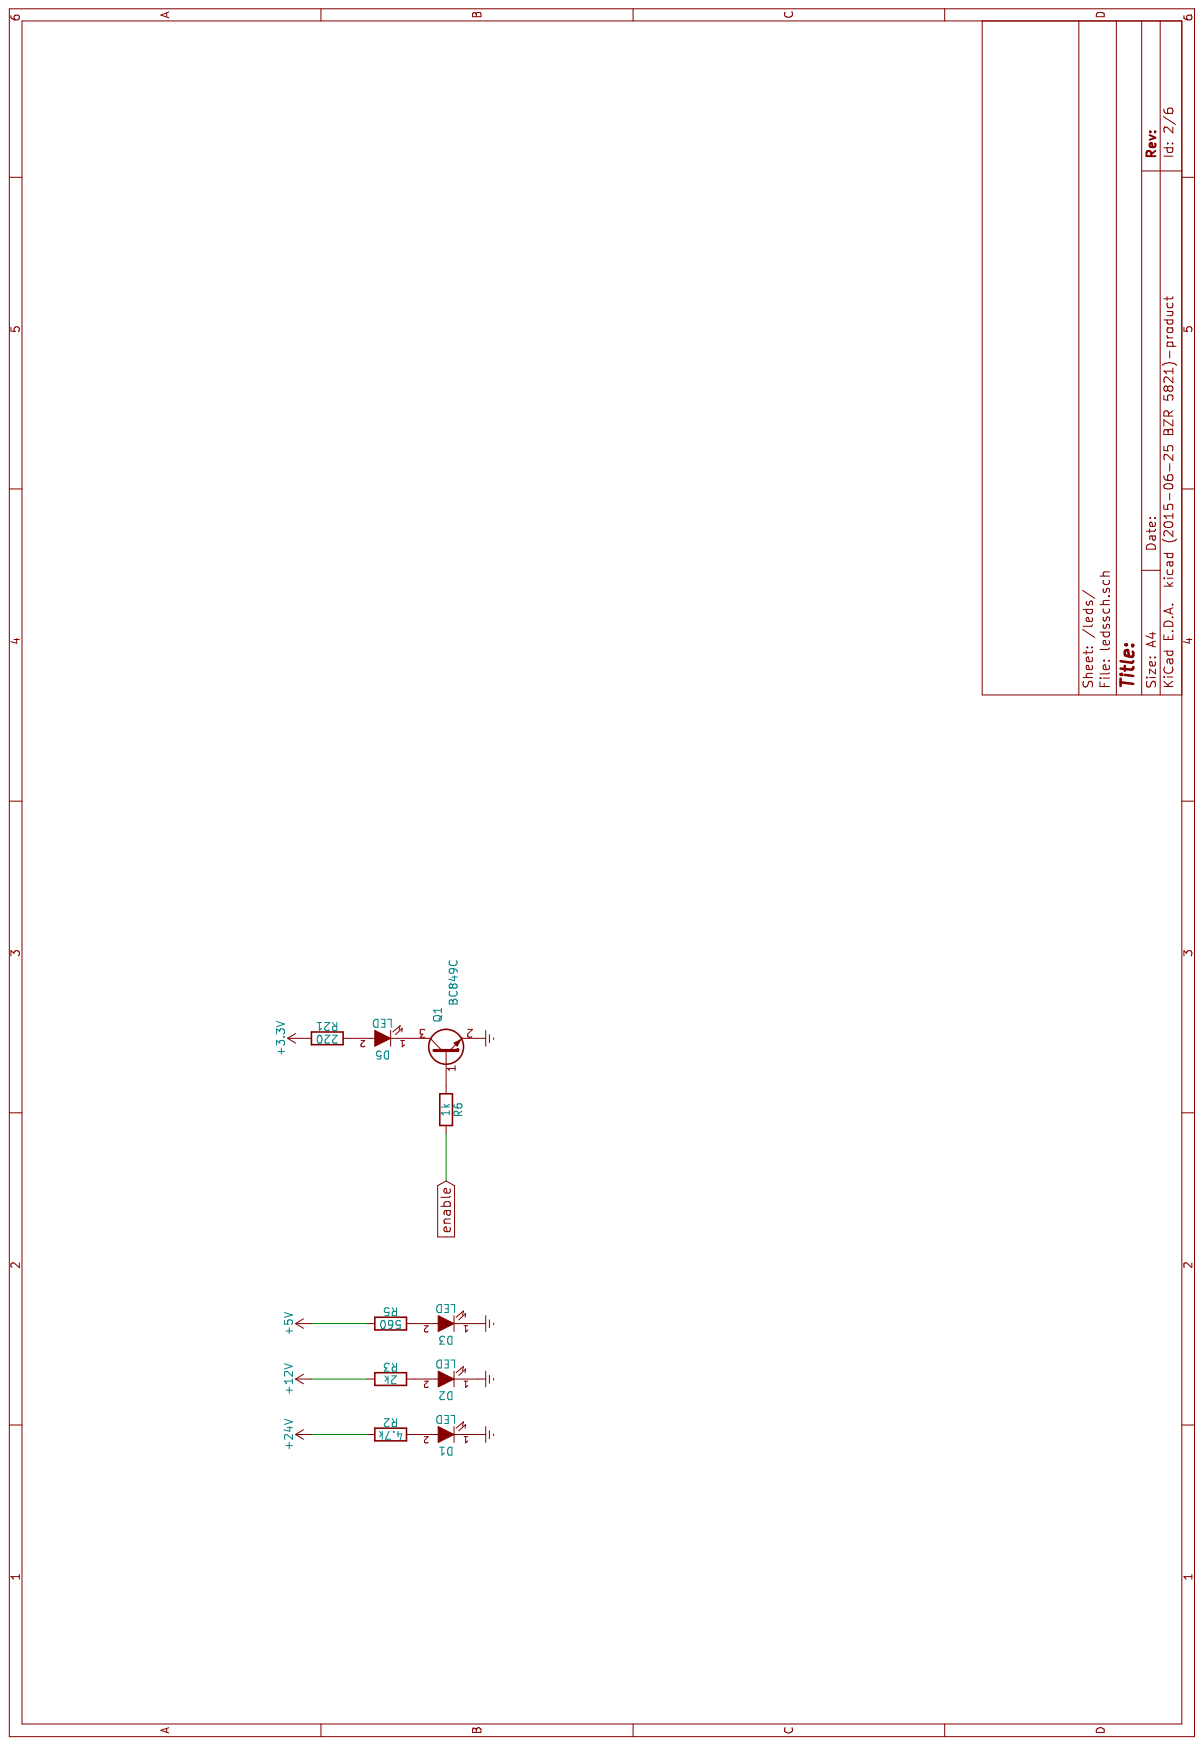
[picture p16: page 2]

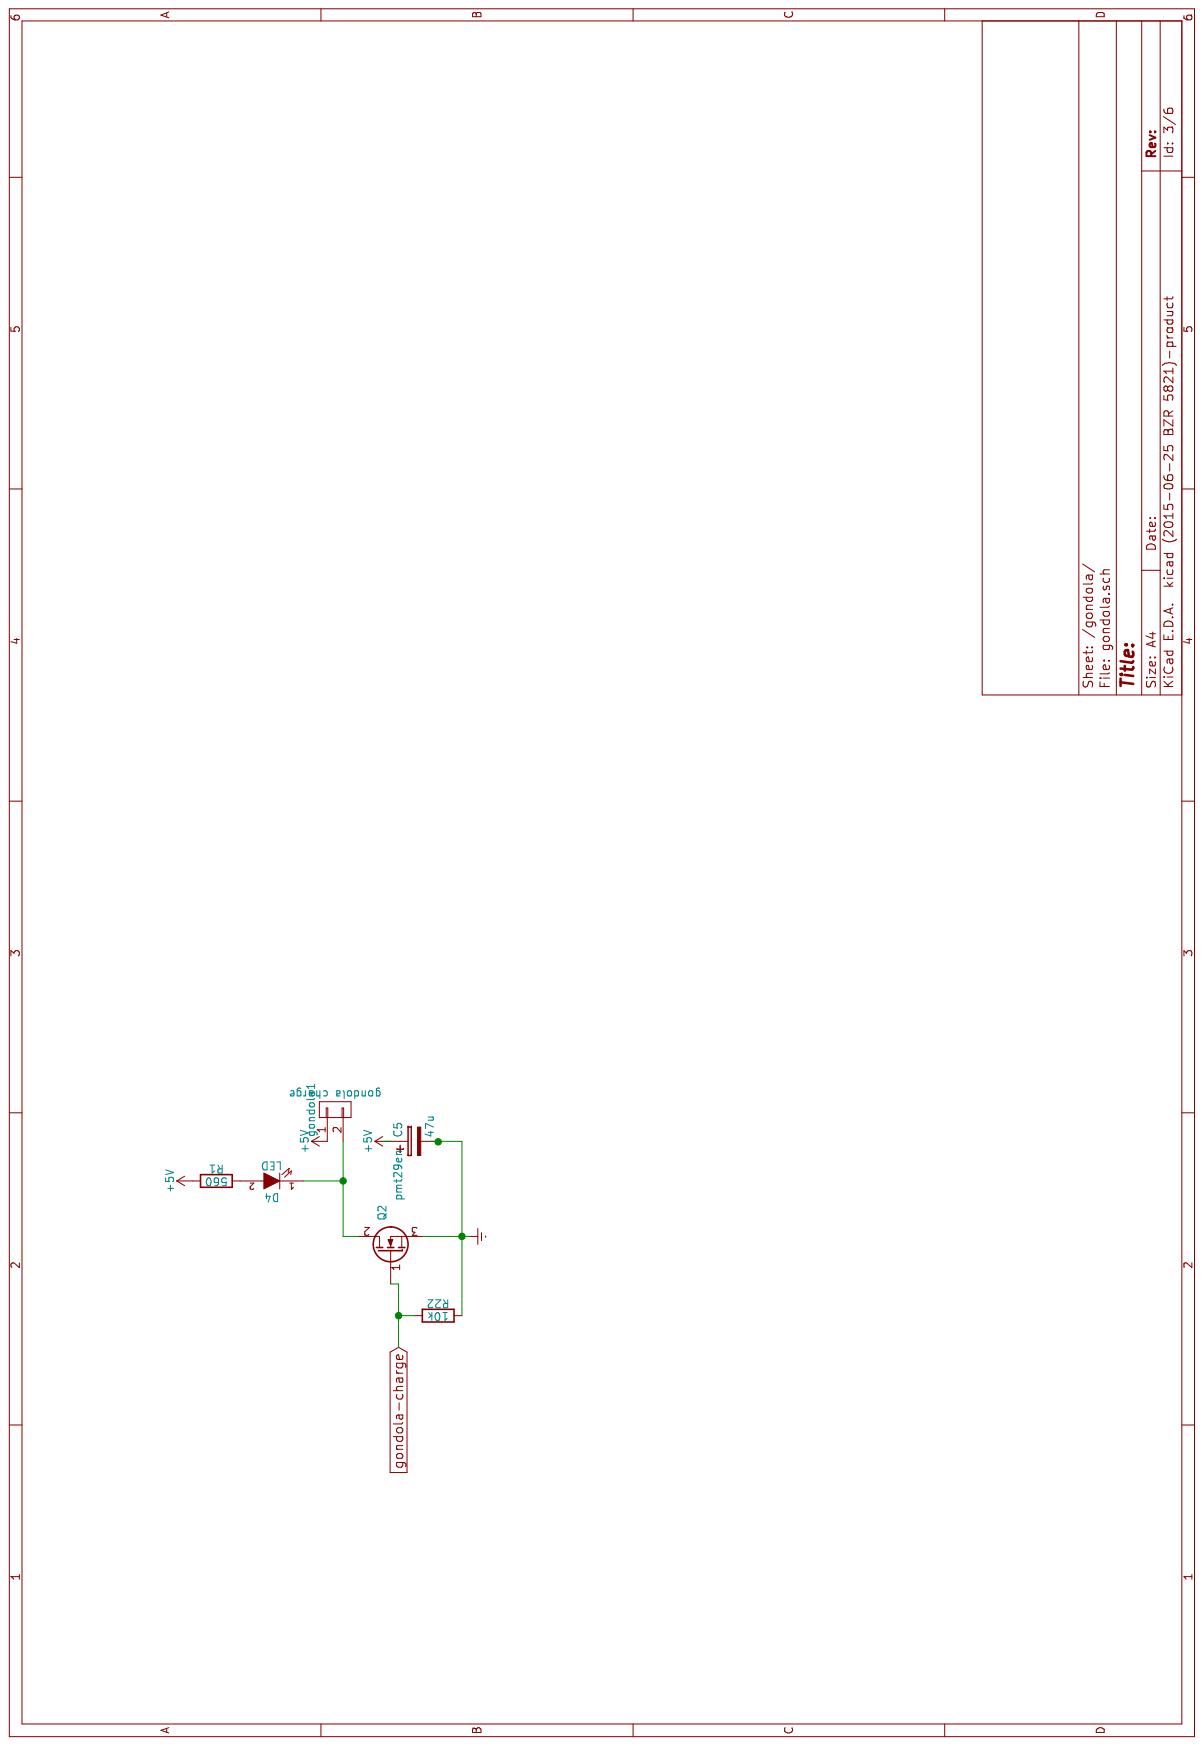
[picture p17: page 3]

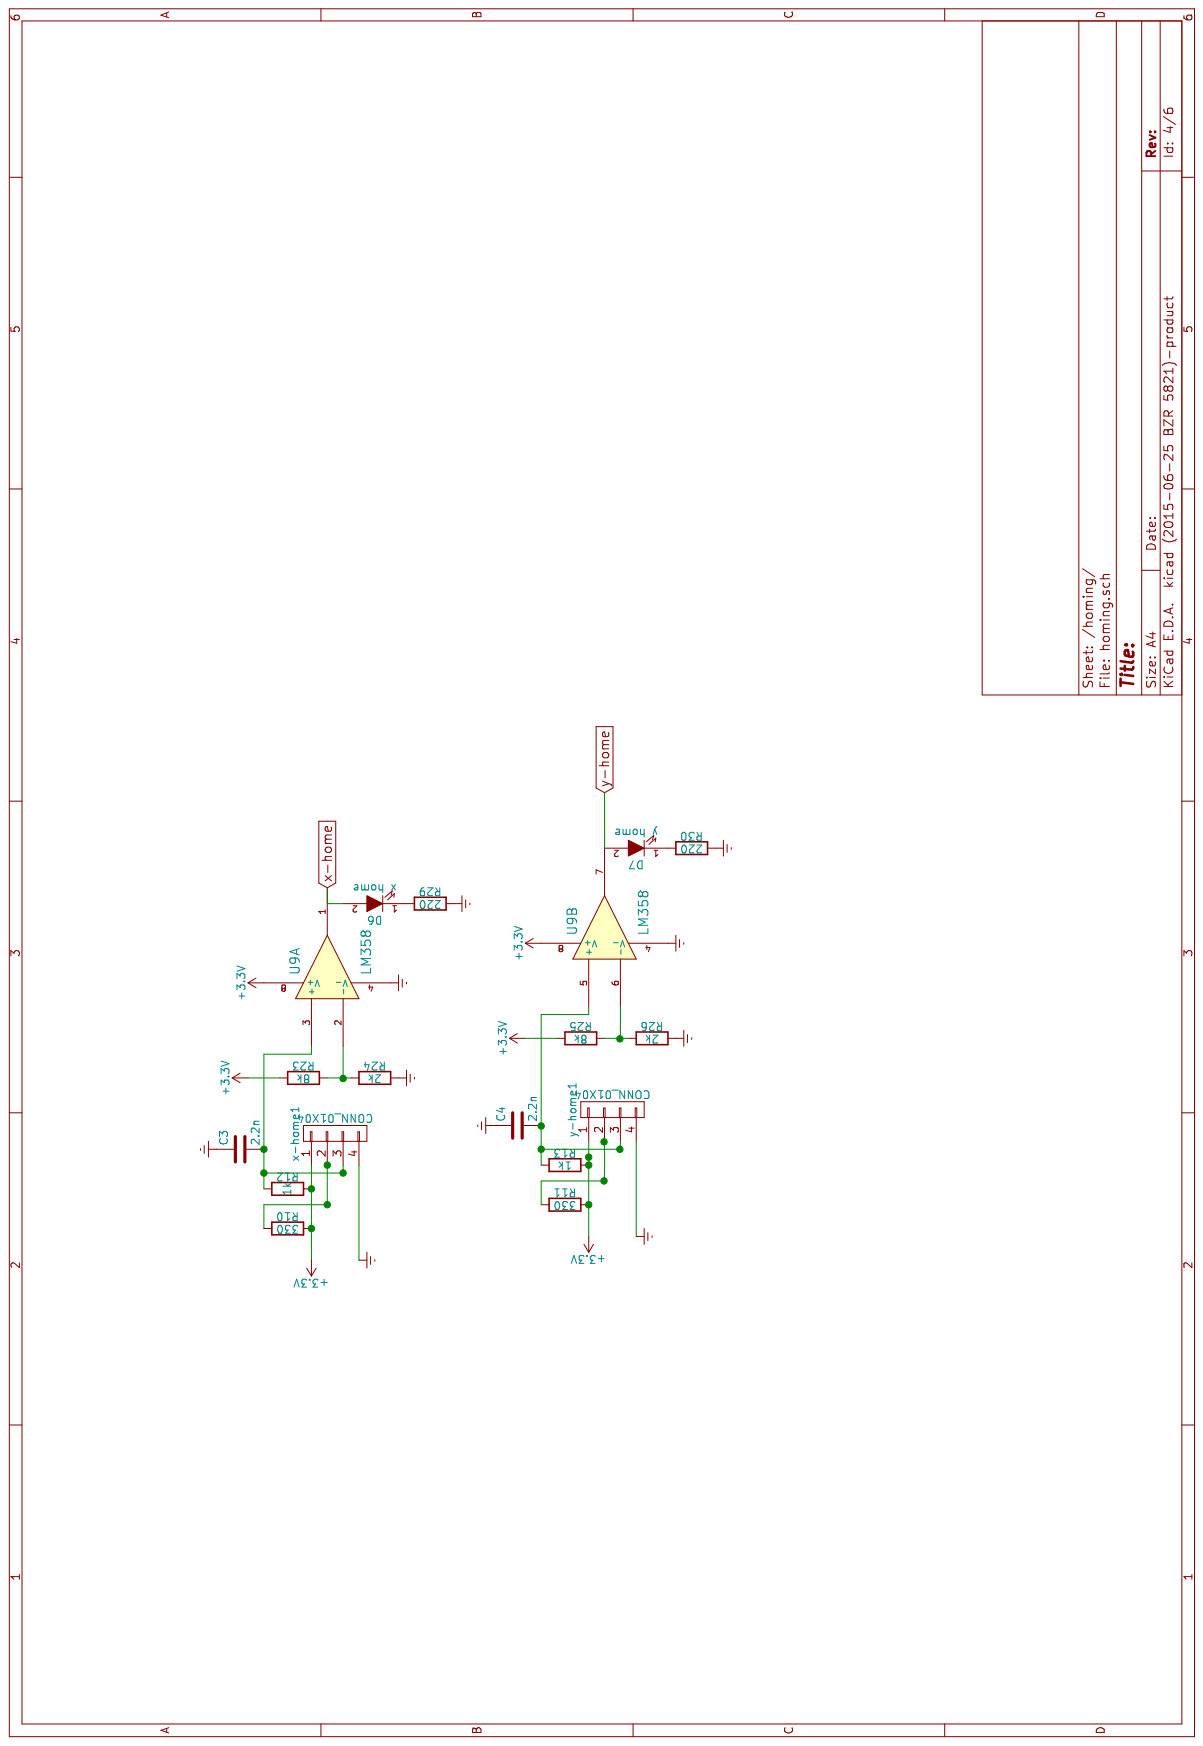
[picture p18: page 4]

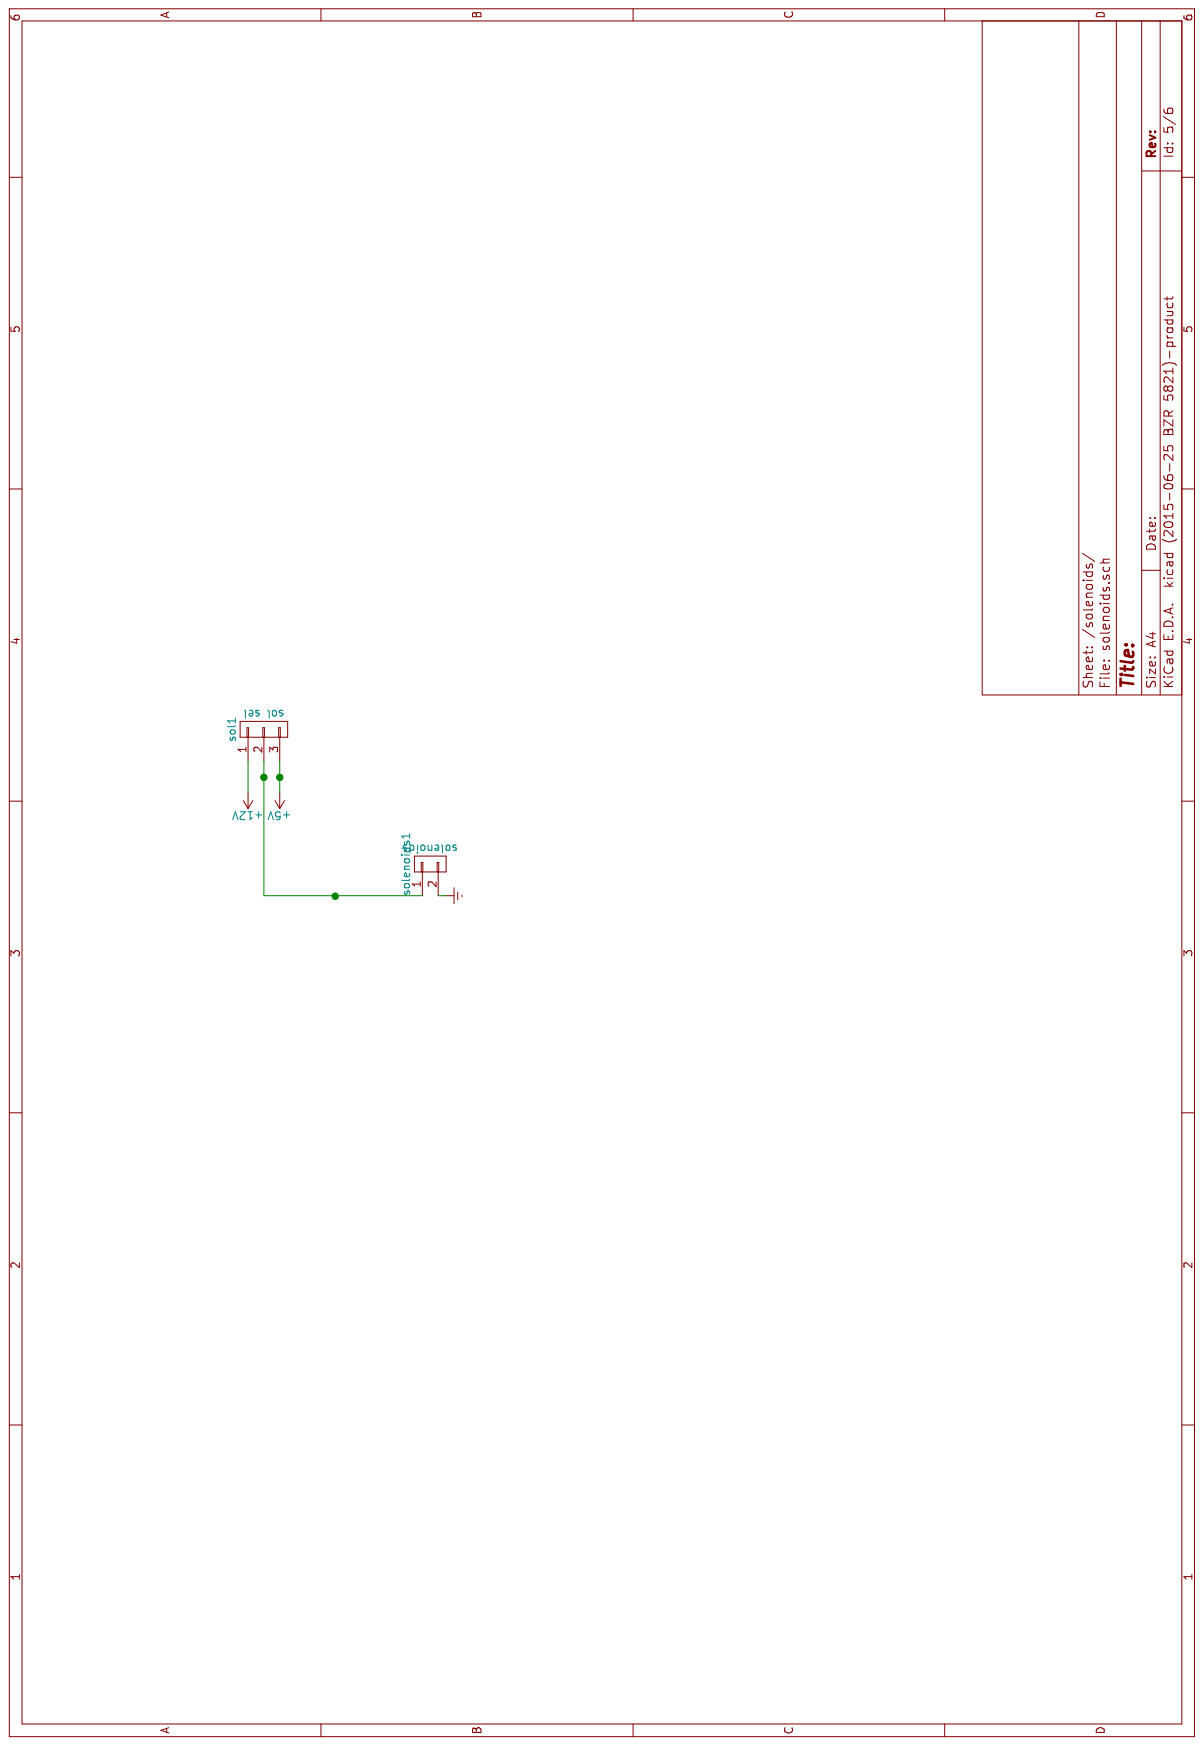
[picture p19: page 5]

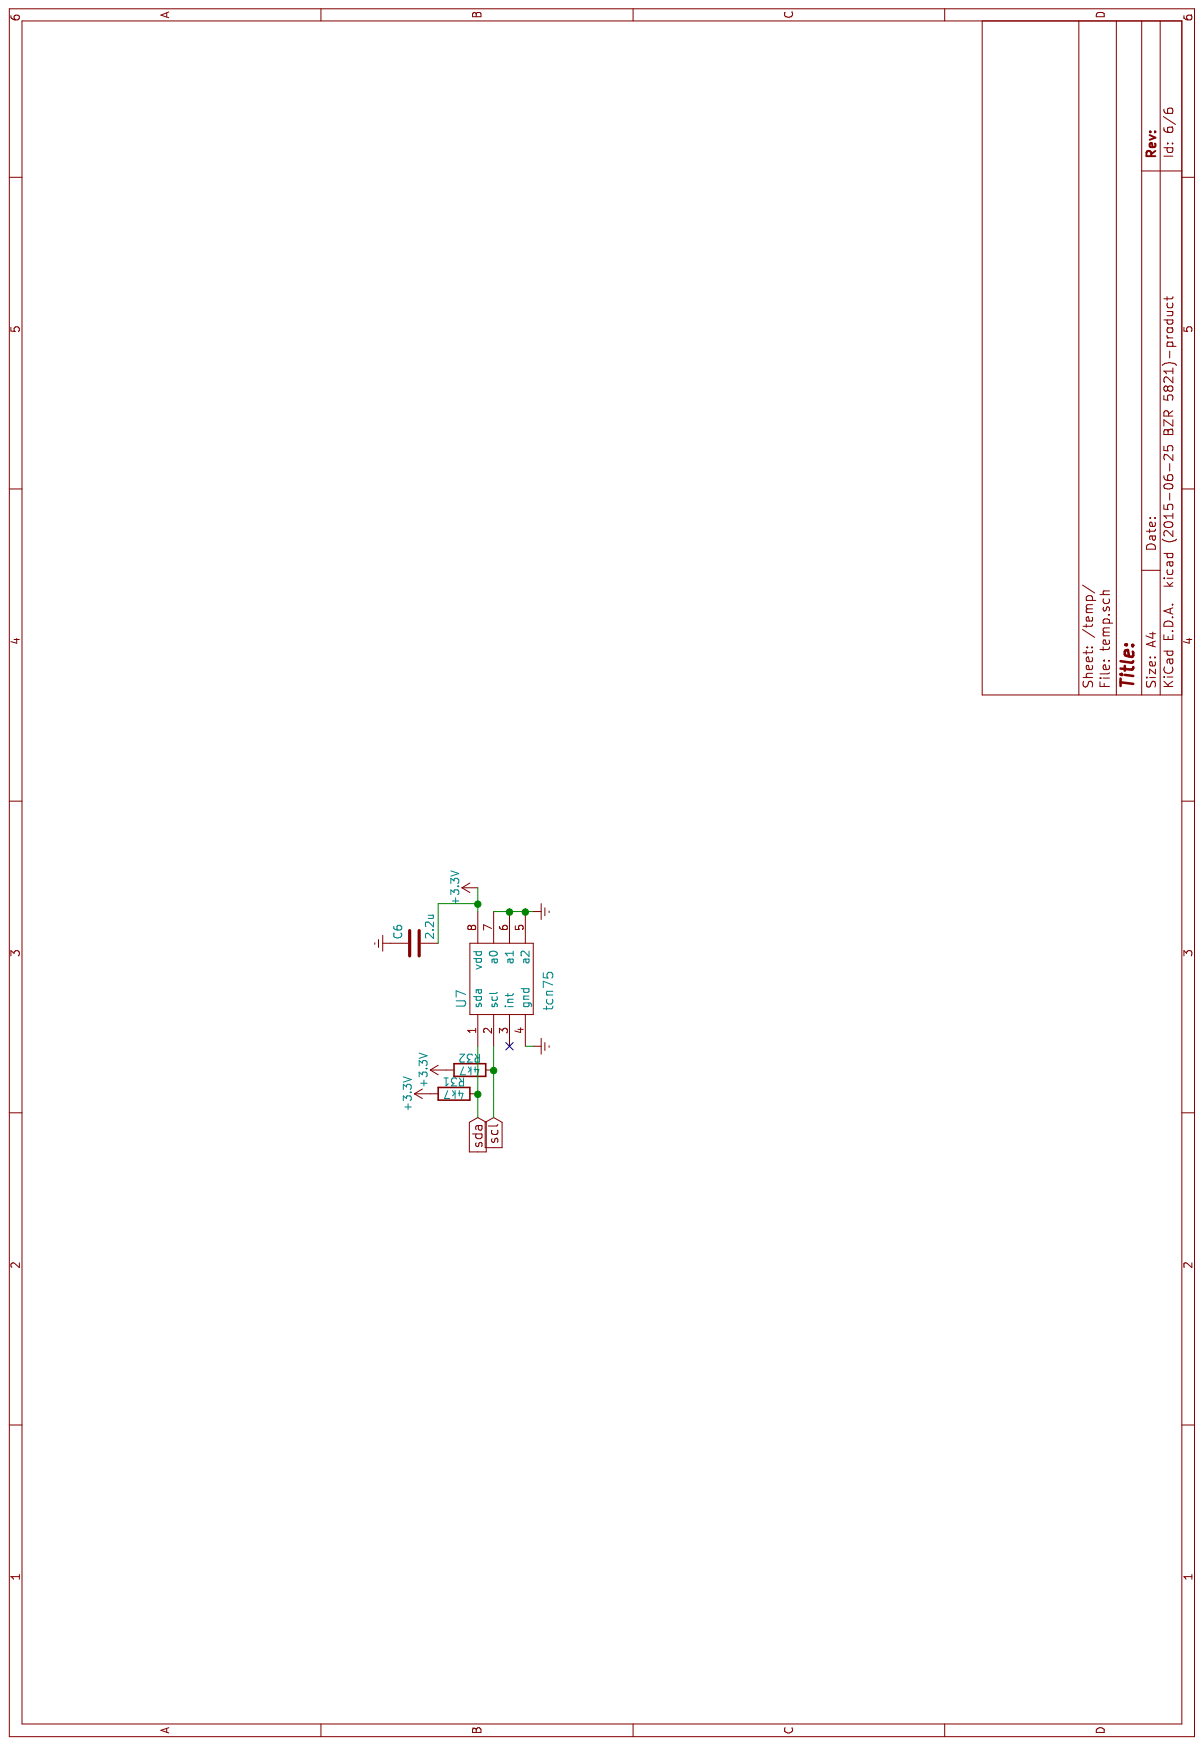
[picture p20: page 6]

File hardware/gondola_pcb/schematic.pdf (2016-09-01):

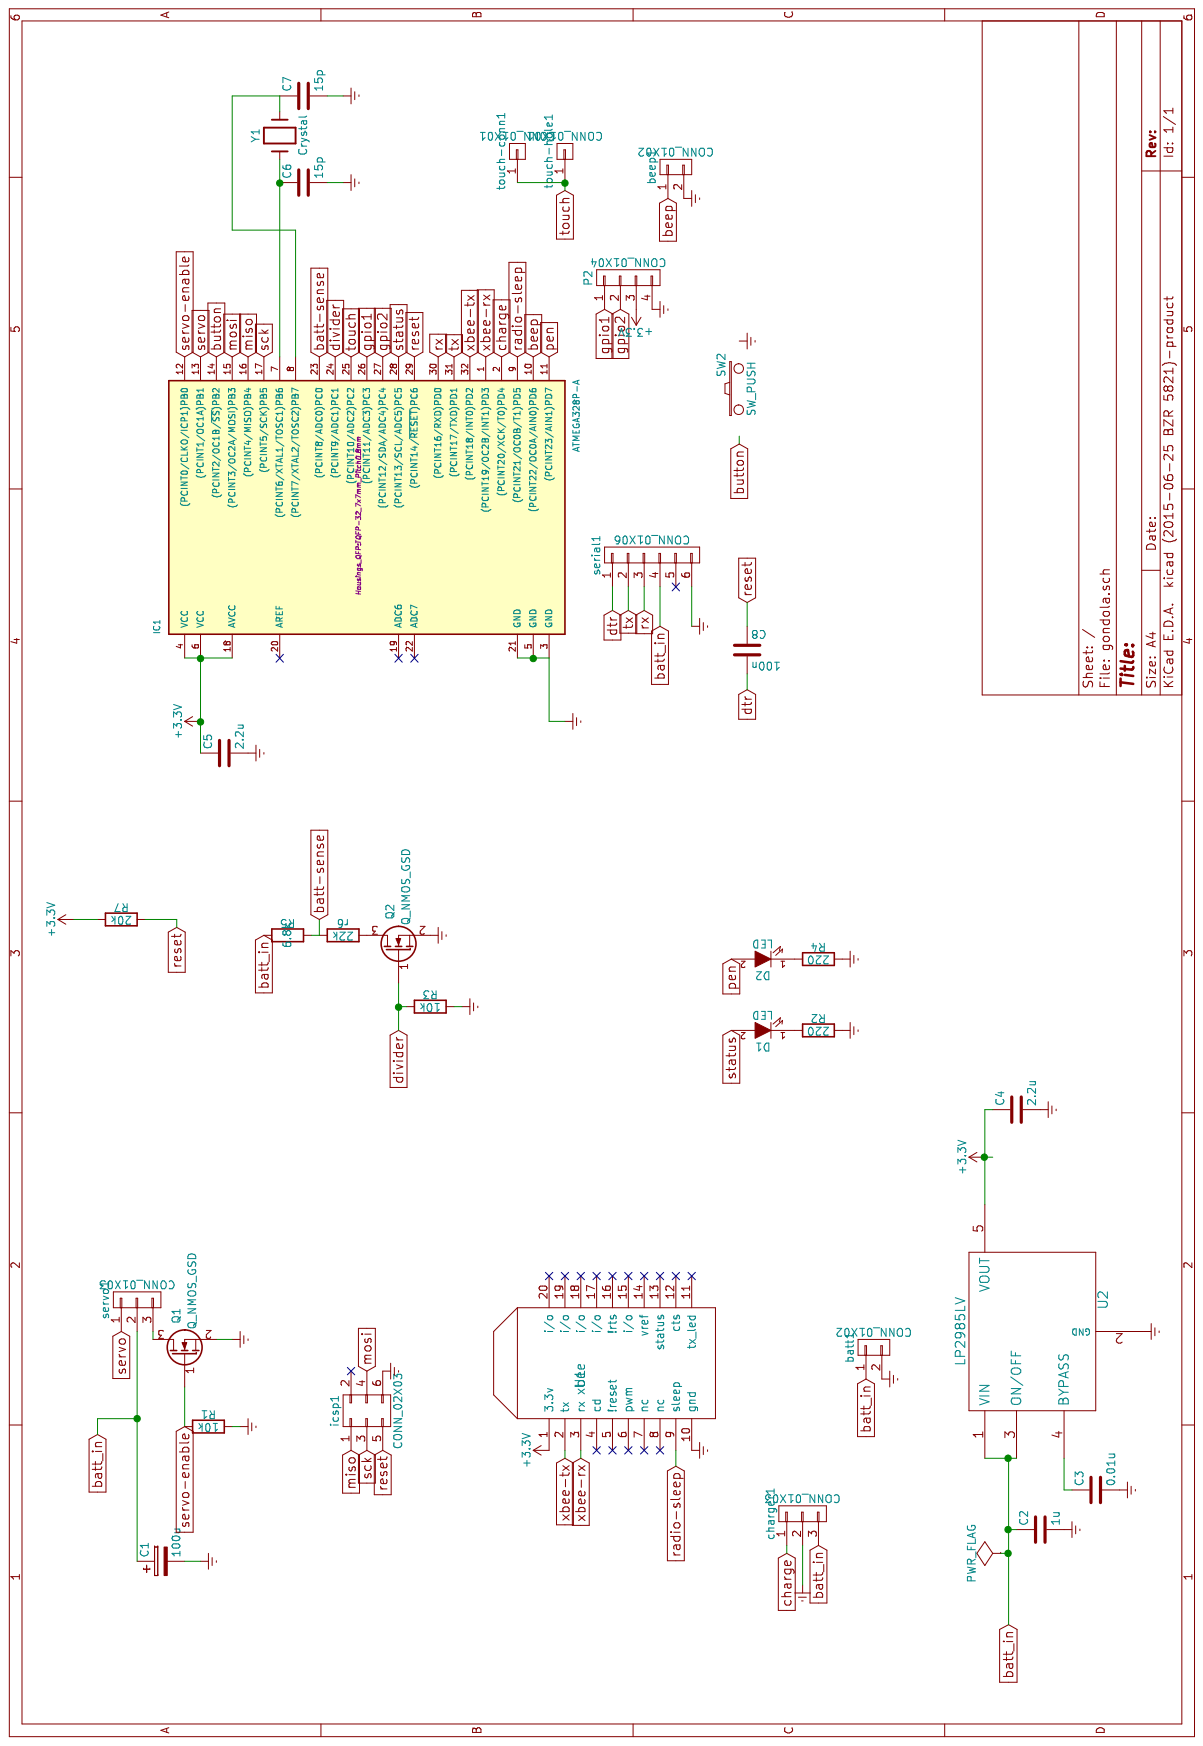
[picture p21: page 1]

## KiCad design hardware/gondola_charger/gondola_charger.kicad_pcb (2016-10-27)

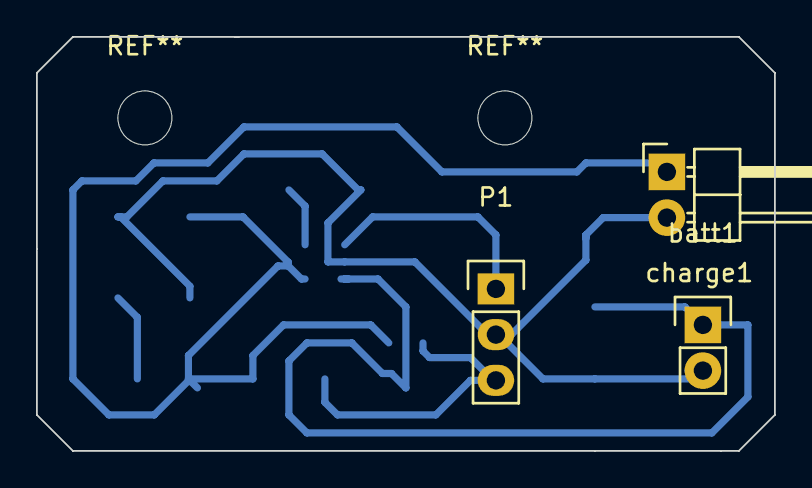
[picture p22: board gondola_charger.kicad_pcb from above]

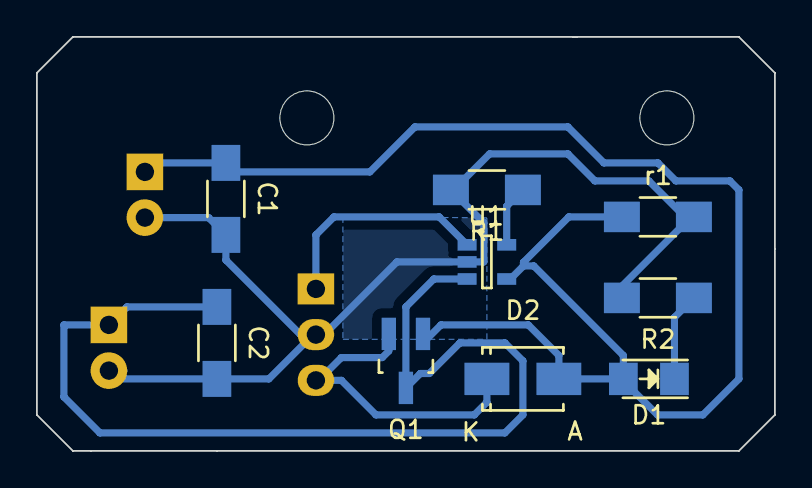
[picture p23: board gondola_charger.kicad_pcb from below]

Board: 2 copper layers, 41.0 x 23.0 mm, 12 parts (9 on the bottom side), 7 nets.

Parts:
C1, C2: 4.7u; C_1206_HandSoldering
D1: LED; LED-1206
D2: D_Schottky; SMA_Standard
P1: board conn; Pin_Header_Straight_1x03
Q1: Q_PMOS_GSD; SOT-23_Handsoldering
R1: 2k; R_1206_HandSoldering
R2: 500r; R_1206_HandSoldering
U1: MCP73832; SOT-23-5
batt1: CONN_01X02; Pin_Header_Straight_1x02
charge1: CONN_01X02; Pin_Header_Angled_1x02
r1: 100k; R_1206_HandSoldering

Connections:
+5V: C1.1, D1.2, D2.2, Q1.1, U1.4, charge1.1, r1.1
GND: C1.2, C2.2, P1.2, R1.2, R2.2, U1.2, batt1.2, charge1.2, r1.2
unnamed: D1.1, R2.1
unnamed: R1.1, U1.5
batt: C2.1, Q1.3, U1.3, batt1.1
charge_safe: P1.1, U1.1
powerout: D2.1, P1.3, Q1.2

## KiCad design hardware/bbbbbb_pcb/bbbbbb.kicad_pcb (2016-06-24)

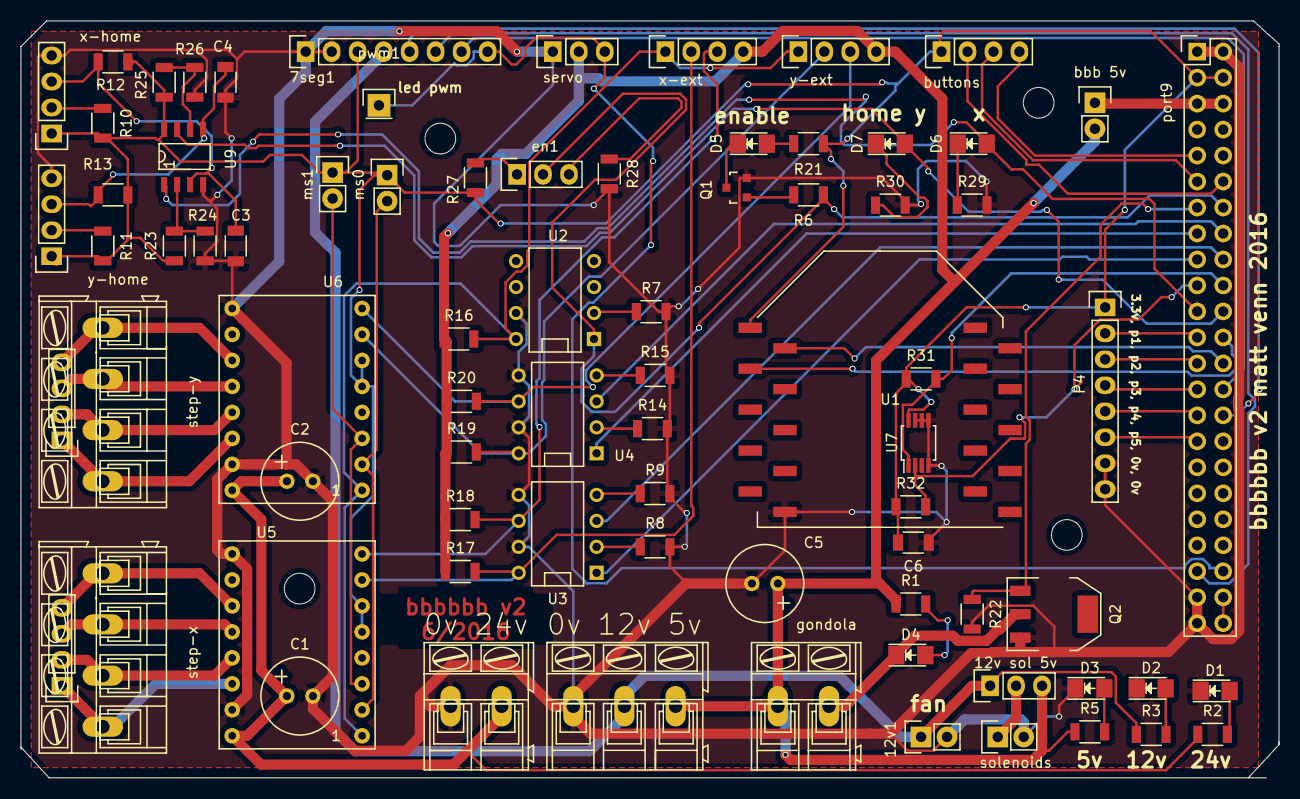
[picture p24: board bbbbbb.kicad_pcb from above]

Board: 2 copper layers, 123.0 x 74.0 mm, 78 parts (0 on the bottom side), 70 nets.

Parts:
0v 12v 5v: 12/5v; AK300-3
0v 24v: 24v; AK300-2
7seg1: 7seg; Pin_Header_Straight_1x08
12v1: fan; Pin_Header_Straight_1x02
12v sol 5v: sol sel; Pin_Header_Straight_1x03
C1, C2: 47uf; Elko_vert_11.2x7.5mm_RM2.5
C3, C4: 2.2n; C_1206
C5: 47u; Elko_vert_11.2x7.5mm_RM2.5
C6: C; C_1206
D1, D2, D3, D4, D5: LED; LED-1206
D6: x home; LED-1206
D7: y home; LED-1206
P4: CONN_01X08; Pin_Header_Straight_1x08
Q1: BC849C; SOT-23
Q2: pmt29en; SOT-223
R1, R5: 560; R_1206
R2: 4.7k; R_1206
R3, R24, R26: 2k; R_1206
R6, R7, R8, R9, R12, R13, R14, R15, R16, R17, R18, R19, R20: 1k; R_1206
R10, R11: 330; R_1206
R21, R29, R30: 220; R_1206
R22, R27, R28: 10k; R_1206
R23, R25: 8k; R_1206
R31, R32: R; R_1206
U1: xbee
U2, U3, U4: LTV-827; DIP-8__300
U5, U6: drv2250; drv8825
U7: tcn75; MSOP-8_3x3mm_Pitch0.65mm
U9: LM358; soic8
bbb 5v: bb-5v; Pin_Header_Straight_1x02
buttons: buttons; Pin_Header_Straight_1x04
en1: enable pull up; Pin_Header_Straight_1x03
gondola: gondola charge; AK300-2
ms0: ms0; Pin_Header_Straight_1x02
ms1: ms1; Pin_Header_Straight_1x02
port9: CONN_02X23; Pin_Header_Straight_2x23
pwm1: CONN_01X01; Pin_Header_Straight_1x01
servo: servo; Pin_Header_Straight_1x03
solenoids: solenoids; Pin_Header_Straight_1x02
step-x: CONN_01X04; AK300-4
step-x2: CONN_01X04; Pin_Header_Straight_1x04
step-y: CONN_01X04; AK300-4
step-y2: CONN_01X04; Pin_Header_Straight_1x04
x-ext: CONN_01X04; Pin_Header_Straight_1x04
x-home: CONN_01X04; Pin_Header_Straight_1x04
y-ext: CONN_01X04; Pin_Header_Straight_1x04
y-home: CONN_01X04; Pin_Header_Straight_1x04

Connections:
+3V3: 7seg1.3, C6.2, P4.1, R10.2, R11.2, R12.2, R13.2, R21.1, R23.1, R25.1, R27.2, R31.1, R32.1, U1.1, U5.5, U5.6, U6.5, U6.6, U7.8, U9.8, buttons.1, ms0.1, ms1.1, port9.3, port9.4, x-home.1, y-home.1
+5V: 0v 12v 5v.3, 12v sol 5v.3, C5.1, R1.1, R5.1, R16.1, R17.1, R18.1, R19.1, R20.1, bbb 5v.2, gondola.1, servo.2, x-ext.4, y-ext.4
+12V: 0v 12v 5v.2, 7seg1.4, 12v1.1, 12v sol 5v.1, R3.1
+24V: 0v 24v.2, C1.1, C2.1, R2.1, U5.16, U6.16
/7seg-!oe: 7seg1.8, port9.42, pwm1.1, servo.3
/7seg-clk: 7seg1.6, port9.41
/7seg-le: 7seg1.7, port9.28
/7seg-sdo: 7seg1.5, port9.30
/bb-5v: bbb 5v.1, port9.5, port9.6
/butt-estop: buttons.3, port9.11
/butt-power: buttons.4, port9.9
/butt-reset: buttons.2, port9.12
/enable-ext: R16.2, U2.8, U5.1, U6.1, x-ext.1, y-ext.1
/gpio1: P4.2, port9.23
/gpio2: P4.3, port9.25
/gpio3: P4.4, port9.27
/gpio4: P4.5, port9.29
/gpio5: P4.6, port9.31
/ms0: U5.2, U6.2, ms0.2
/ms1: U5.3, U6.3, ms1.2
/xbee-rx: U1.3, port9.24
/xbee-tx: U1.2, port9.26
/xdir: U3.3, port9.18
/xdir-ext: R18.2, U3.6, U5.8, x-ext.3
/xstep: U3.1, port9.17
/xstep-ext: R17.2, U3.8, U5.7, x-ext.2
/ydir: U4.3, port9.16
/ydir-ext: R20.2, U4.6, U6.8, y-ext.3
/ystep: U4.1, port9.15
/ystep-ext: R19.2, U4.8, U6.7, y-ext.2
Earth: 0v 12v 5v.1, 0v 24v.1, 7seg1.1, 7seg1.2, 12v1.2, C1.2, C2.2, C3.1, C4.1, C5.2, C6.1, D1.1, D2.1, D3.1, P4.7, P4.8, Q1.2, Q2.3, R7.2, R8.2, R9.2, R14.2, R15.2, R22.2, R24.2, R26.2, R28.2, R29.2, R30.2, U1.10, U2.7, U3.5, U3.7, U4.5, U4.7, U5.9, U5.15, U6.9, U6.15, U7.4, U7.5, U7.6, U7.7, U9.4, port9.1, port9.2, port9.43, port9.45, servo.1, solenoids.2, x-home.4, y-home.4
unnamed: C3.2, R12.1, U9.3, x-home.3
unnamed: C4.2, R13.1, U9.5, y-home.3
unnamed: D1.2, R2.2
unnamed: D2.2, R3.2
unnamed: D3.2, R5.2
unnamed: D4.1, Q2.2, gondola.2
unnamed: D4.2, R1.2
unnamed: D5.1, Q1.3
unnamed: D5.2, R21.2
unnamed: D6.1, R29.1
unnamed: D7.1, R30.1
unnamed: Q1.1, R6.1
unnamed: R7.1, U2.2
unnamed: R8.1, U3.2
unnamed: R9.1, U3.4
unnamed: R10.1, x-home.2
unnamed: R11.1, y-home.2
unnamed: R14.1, U4.2
unnamed: R15.1, U4.4
unnamed: R23.2, R24.1, U9.2
unnamed: R25.2, R26.1, U9.6
unnamed: R27.1, en1.1
unnamed: R28.1, en1.3
unnamed: U5.11, step-x.4, step-x2.4
unnamed: U5.12, step-x.3, step-x2.3
unnamed: U5.13, step-x.2, step-x2.2
unnamed: U5.14, step-x.1, step-x2.1
unnamed: U6.11, step-y.4, step-y2.4
unnamed: U6.12, step-y.3, step-y2.3
unnamed: U6.13, step-y.2, step-y2.2
unnamed: U6.14, step-y.1, step-y2.1
unnamed: port9.44, port9.46
unnamed: 12v sol 5v.2, solenoids.1
enable: R6.2, U2.1, en1.2, port9.14
gondola-charge: Q2.1, R22.1, port9.13
scl: R32.2, U7.2, port9.19
sda: R31.2, U7.1, port9.20
x-home: D6.2, U9.1, port9.21
y-home: D7.2, U9.7, port9.22

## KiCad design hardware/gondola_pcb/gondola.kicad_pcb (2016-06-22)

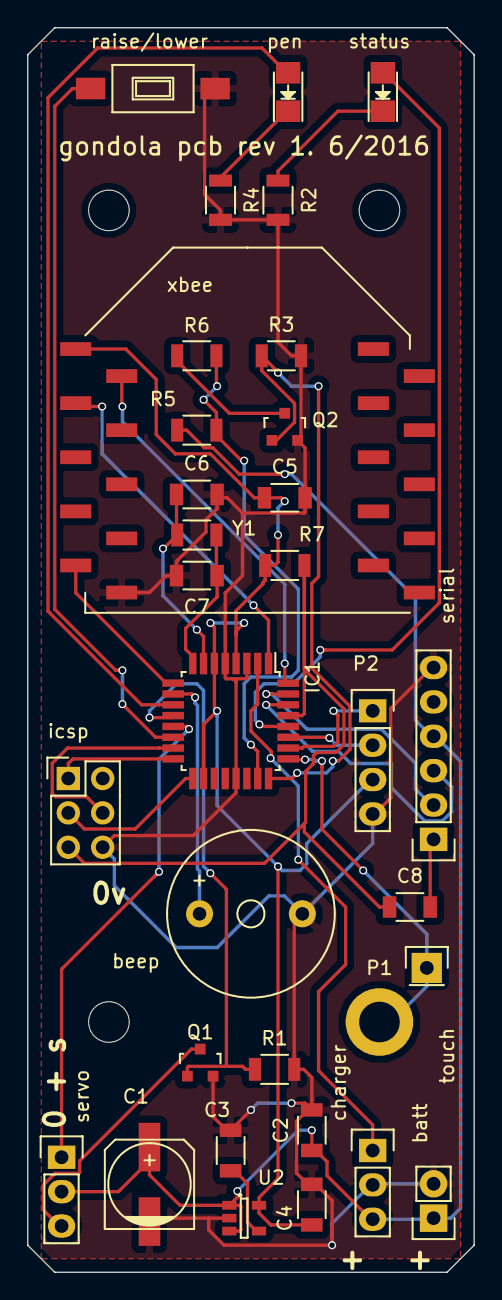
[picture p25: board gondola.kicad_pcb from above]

Board: 2 copper layers, 33.0 x 92.0 mm, 33 parts (0 on the bottom side), 32 nets.

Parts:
C1: 100u; c_elec_6.3x5.3
C2: 1u; C_1206
C3: 0.01u; C_1206
C4, C5: 2.2u; C_1206
C6, C7: 20p; C_1206
C8: 100n; C_1206
IC1: ATMEGA328P-A; TQFP-32_7x7mm_Pitch0.8mm
P1: CONN_01X01; MountingHole_3mm
P2: CONN_01X04; Pin_Header_Straight_1x04
Q1, Q2: Q_NMOS_GSD; SOT-23
R1, R3: 10k; R_1206
R2, R4, R5, R6: R; R_1206
R7: 20k; R_1206
U2: LP2985LV; SOT-23-5
Y1: Crystal; R_1206
batt: CONN_01X02; Pin_Header_Straight_1x02
beep: CONN_01X02; Buzzer_12x9.5RM7.6
charger: CONN_01X03; Pin_Header_Straight_1x03
icsp: CONN_02X03; Pin_Header_Straight_2x03
pen: LED; LED-1206
raise/lower: SW_PUSH; SW_SPST_FSMSM
serial: CONN_01X06; Pin_Header_Straight_1x06
servo: CONN_01X03; Pin_Header_Straight_1x03
status: LED; LED-1206
touch: CONN_01X01; Pin_Header_Straight_1x01
xbee: xbee

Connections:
+3V3: C4.1, C5.1, IC1.4, IC1.6, IC1.18, P2.3, R7.1, U2.5, xbee.1
Earth: C1.2, C2.2, C3.2, C4.2, C5.2, C6.2, C7.2, IC1.3, IC1.5, IC1.21, P2.4, Q1.2, Q2.2, R1.2, R2.2, R3.2, R4.2, U2.2, batt.2, beep.2, charger.2, icsp.6, raise/lower.2, serial.6, xbee.10
unnamed: C3.1, U2.4
unnamed: C6.1, IC1.7, Y1.1
unnamed: C7.1, IC1.8, Y1.2
unnamed: R2.1, status.1
unnamed: R4.1, pen.1
unnamed: Q1.3, servo.3
unnamed: Q2.3, R6.2
batt-sense: IC1.23, R5.2, R6.1
batt_in: C1.1, C2.1, R5.1, U2.1, U2.3, batt.1, charger.3, serial.4, servo.2
beep: IC1.10, beep.1
button: IC1.14, raise/lower.1
charge: IC1.2, charger.1
divider: IC1.24, Q2.1, R3.1
dtr: C8.2, serial.1
gpio1: IC1.26, P2.1
gpio2: IC1.27, P2.2
miso: IC1.16, icsp.1
mosi: IC1.15, icsp.4
pen: IC1.11, pen.2
radio-sleep: IC1.9, xbee.9
reset: C8.1, IC1.29, R7.2, icsp.5
rx: IC1.30, serial.3
sck: IC1.17, icsp.3
servo: IC1.13, servo.1
servo-enable: IC1.12, Q1.1, R1.1
status: IC1.28, status.2
touch: IC1.25, P1.1, touch.1
tx: IC1.31, serial.2
xbee-rx: IC1.1, xbee.3
xbee-tx: IC1.32, xbee.2

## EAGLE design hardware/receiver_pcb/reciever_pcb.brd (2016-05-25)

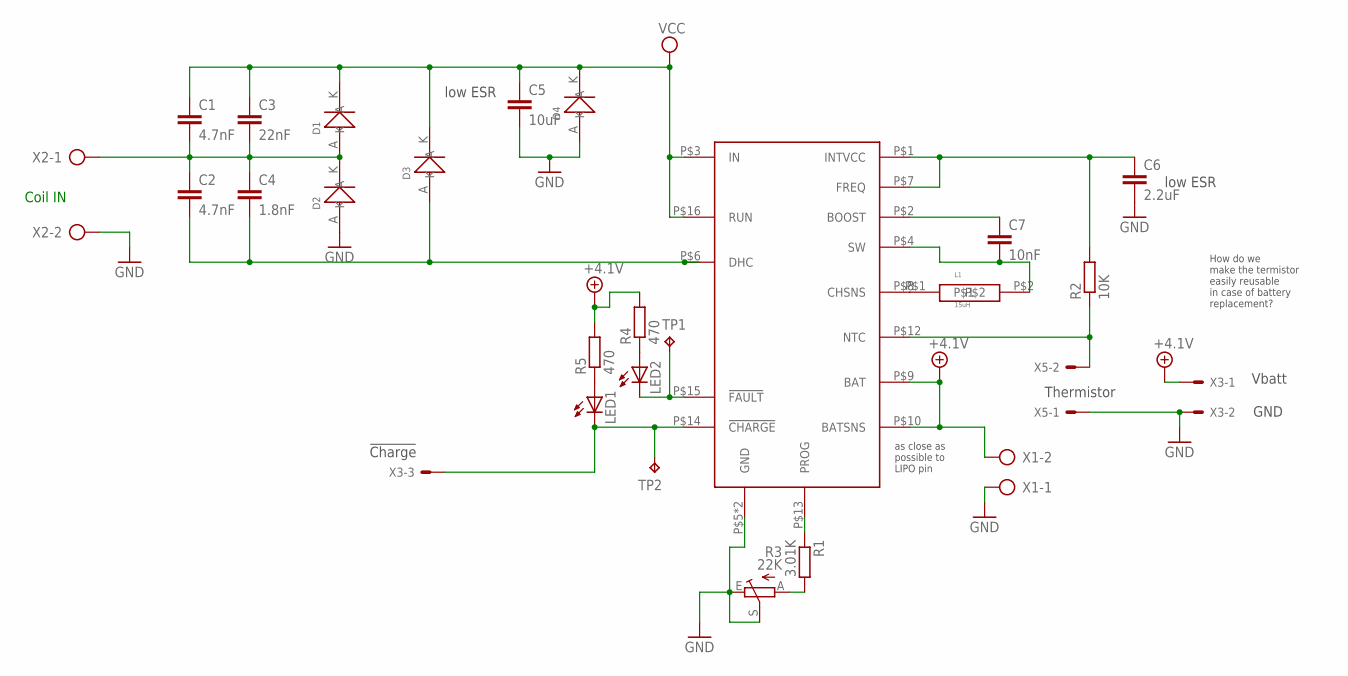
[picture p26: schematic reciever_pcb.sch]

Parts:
C1, C2: 4.7nF; C0805
C3: 22nF; C0805
C4: 1.8nF; C0805
C5: 10uF; C0805
C6: 2.2uF; C0805
C7: 10nF; C0805
D1, D2, D3: DFLS240L; POWERDI123
D4: 39VZ; POWERDI123
L1: 15uH; D62LCB
LED1, LED2: LEDCHIP-LED0805; CHIP-LED0805
R1: 3.01K; R0805
R2: 10K; R0805
R3: 22K; S63S
R4, R5: 470; R0805
TP1, TP2: TPTP19R; TP19R
U$1: LT4120; QFN16
X1, X2: AK500/2
X3: KK-156-3
X5: KK-156-2

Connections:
+4.1V: R4.2, R5.2, U$1.P$9 (BAT), U$1.P$10 (BATSNS), X1.2, X3.1
GND: C5.2, C6.2, D2.A, D4.A, R3.E, R3.S, U$1.P$5 (GND), U$1.P$17 (GND), X1.1, X2.2, X3.2, X5.1
unnamed: C1.2, C2.1, C3.2, C4.1, D1.A, D2.K, X2.1
unnamed: C2.2, C4.2, D3.A, U$1.P$6 (DHC)
unnamed: C6.1, R2.2, U$1.P$1 (INTVCC), U$1.P$7 (FREQ)
unnamed: C7.1, U$1.P$2 (BOOST)
unnamed: C7.2, L1.P$2, U$1.P$4 (SW)
unnamed: L1.P$1, U$1.P$8 (CHSNS)
unnamed: R1.1, U$1.P$13 (PROG)
unnamed: R2.1, U$1.P$12 (NTC), X5.2
unnamed: LED1.C, TP2.TP, U$1.P$14 (!CHARGE), X3.3
unnamed: LED2.A, R4.1
unnamed: LED1.A, R5.1
unnamed: R1.2, R3.A
unnamed: LED2.C, TP1.TP, U$1.P$15 (!FAULT)
VCC: C1.1, C3.1, C5.1, D1.K, D3.K, D4.K, U$1.P$3 (IN), U$1.P$16 (RUN)

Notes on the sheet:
Coil IN
low ESR
as close as possible to LIPO pin
How do we make the termistor easily reusable in case of battery replacement?
!Charge
Vbatt
GND
Thermistor

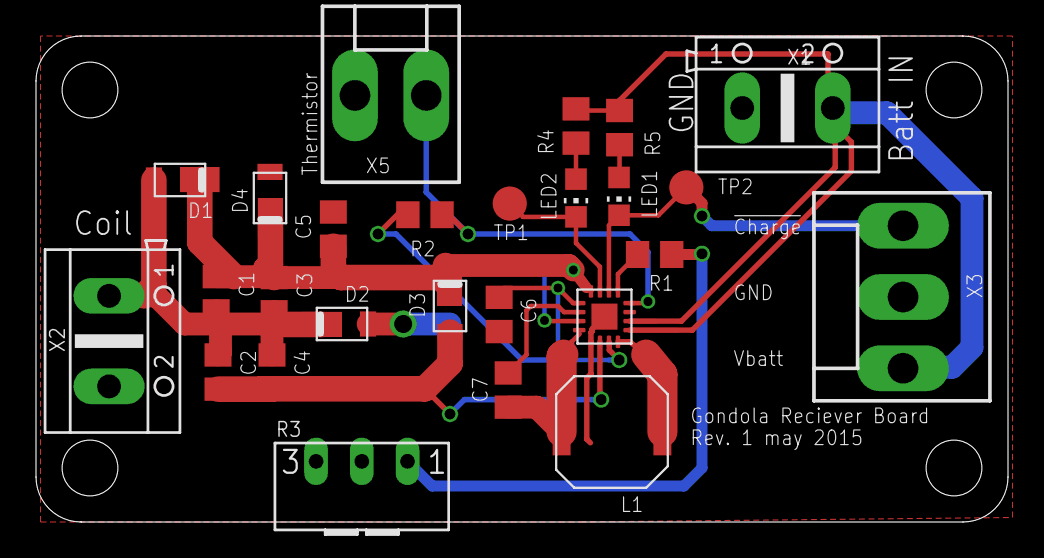
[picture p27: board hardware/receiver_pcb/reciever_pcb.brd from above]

Board: 2 copper layers, 54.0 x 27.0 mm, 26 parts (0 on the bottom side), 16 nets.

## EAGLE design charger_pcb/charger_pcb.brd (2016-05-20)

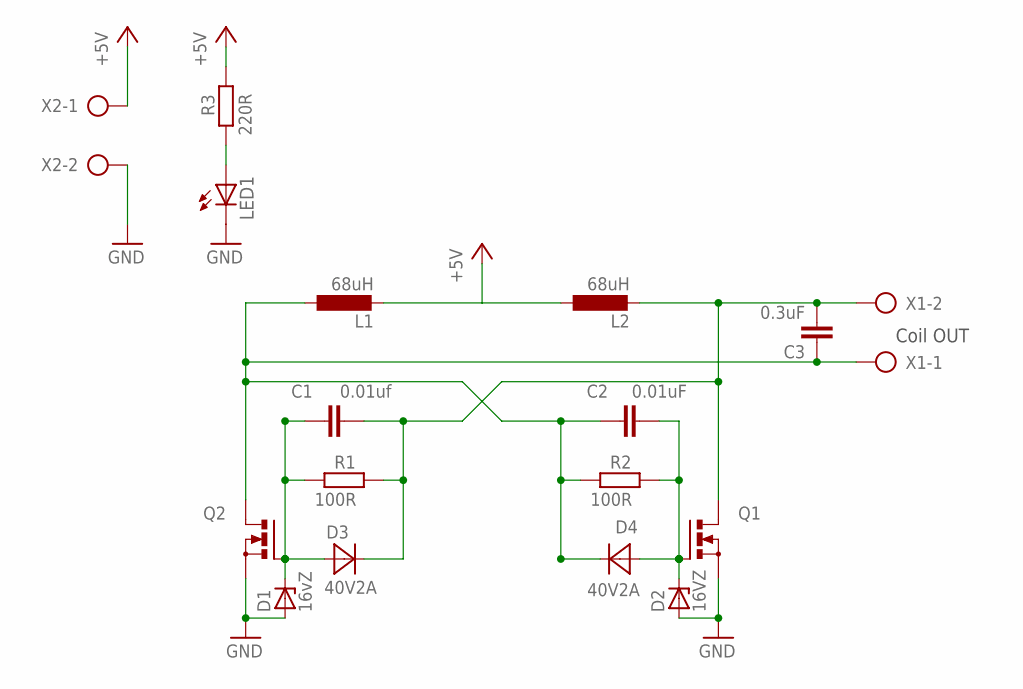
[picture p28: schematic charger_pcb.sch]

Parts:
C1: 0.01uf; C0805
C2: 0.01uF; C0805
C3: 0.3uF; C0805
D1: 16vZ; SOD80C
D2: 16VZ; SOD80C
D3, D4: 40V2A; SMA
L1, L2: 68uH; L5650M
LED1: LEDCHIP-LED0805; CHIP-LED0805
Q1, Q2: N-MOSFET-SO8S; SO-08
R1, R2: 100R; R0805
R3: 220R; R0805
X1, X2: AK500/2

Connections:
+5V: L1.2, L2.1, R3.2, X2.1
GND: D1.A, D2.A, LED1.C, Q1.1 (S), Q1.2 (S), Q1.3 (S), Q2.1 (S), Q2.2 (S), Q2.3 (S), X2.2
unnamed: C1.1, D1.C, D3.A, Q2.4 (G), R1.1
unnamed: C1.2, C3.2, D3.C, L2.2, Q1.5 (D), Q1.6 (D), Q1.7 (D), Q1.8 (D), R1.2, X1.2
unnamed: C2.2, D2.C, D4.A, Q1.4 (G), R2.2
unnamed: C2.1, C3.1, D4.C, L1.1, Q2.5 (D), Q2.6 (D), Q2.7 (D), Q2.8 (D), R2.1, X1.1
unnamed: LED1.A, R3.1

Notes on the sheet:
Coil OUT

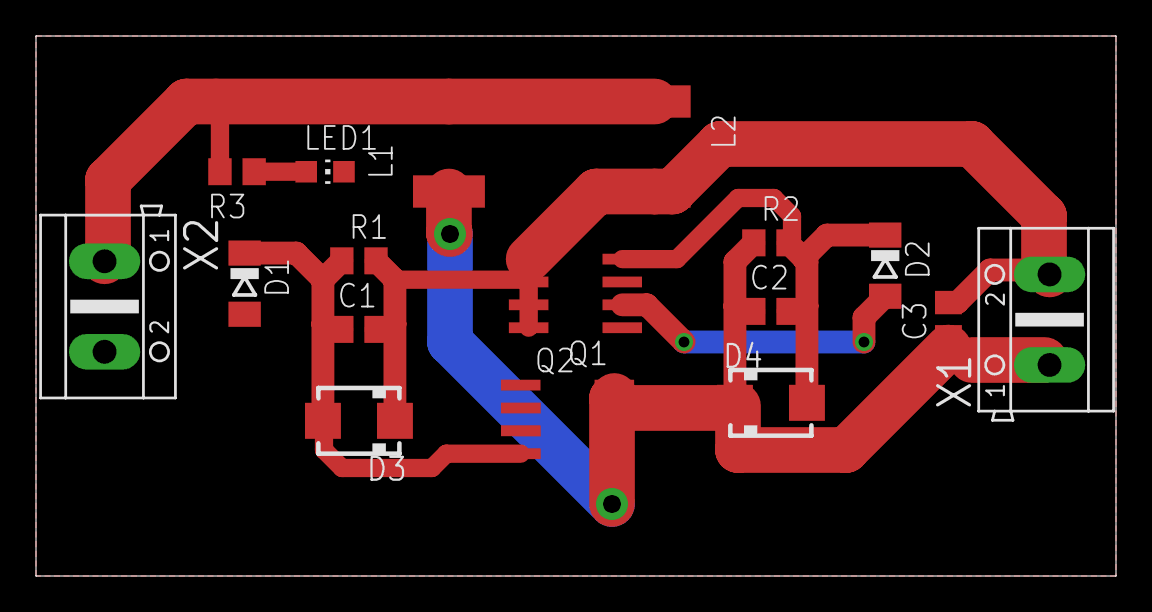
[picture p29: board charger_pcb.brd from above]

Board: 2 copper layers, 60.0 x 30.0 mm, 17 parts (0 on the bottom side), 7 nets.

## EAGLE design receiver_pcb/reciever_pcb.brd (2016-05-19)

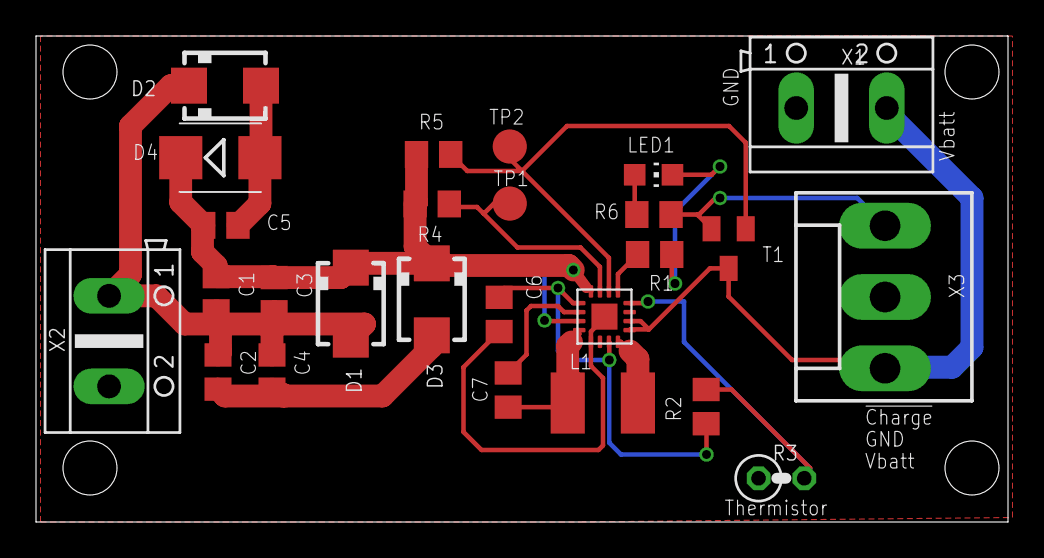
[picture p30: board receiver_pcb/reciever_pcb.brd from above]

Board: 2 copper layers, 54.0 x 27.0 mm, 26 parts (0 on the bottom side), 15 nets.

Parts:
C1, C2: 4.7nF; C0805
C3: 22nF; C0805
C4: 1.8nF; C0805
C5: 10uF; C0805
C6: 2.2uF; C0805
C7: 10nF; C0805
D1, D2, D3: 40V 2A; SMA
D4: 39V; SMB
L1: 15uH; L1812
LED1: CHIP-LED0805
R1: 3.01K; R0805
R2, R4, R5: 10K; R0805
R3: thermistor; 0207/2V
R6: 220; R0805
T1: SOT23-BCE
TP1, TP2: TPTP19R; TP19R
U$1: LT4120; QFN16
X1, X2: AK500/2
X3: KK-156-3

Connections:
+4.1V: T1.E, U$1.P$9, U$1.P$10, X1.2, X3.1
GND: C5.2, C6.2, D2.A, D4.A, LED1.C, R1.2, R3.1, U$1.P$5, U$1.P$17, X1.1, X2.2, X3.2
unnamed: C1.2, C2.1, C3.2, C4.1, D1.A, D2.C, X2.1
unnamed: C2.2, C4.2, D3.A
unnamed: C6.1, R2.2, U$1.P$1, U$1.P$7
unnamed: C7.1, U$1.P$2
unnamed: C7.2, L1.1, U$1.P$4
unnamed: L1.2, U$1.P$8
unnamed: R1.1, U$1.P$13
unnamed: R2.1, R3.2, U$1.P$12
unnamed: R5.1, T1.B, TP2.TP, U$1.P$14
unnamed: R4.1, TP1.TP, U$1.P$15
unnamed: LED1.A, R6.1
unnamed: R6.2, T1.C, X3.3
VCC: C1.1, C3.1, C5.1, D1.C, D3.C, D4.C, R4.2, R5.2, U$1.P$3, U$1.P$16

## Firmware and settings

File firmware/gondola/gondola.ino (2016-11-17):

//#include <SoftwareSerial.h>
#include <Servo.h>

#define LED_PEN 7
#define LED_STATUS A5
#define BEEP 6
#define XBEE_SLEEP 5

#define SERVO_ENABLE 8
#define SERVO 9
#define BUTTON 10

#define BATT_SENSE A0
#define BATT_DIVIDER A1
#define TOUCH A2
#define CHARGE 4

#define SERVO_MAX 160 //startup servo position hitec hs-81
#define SERVO_MIN 20
#define MON_INTERVAL 1000 //delay between reading ADC

#define AVG_NUM 10000 //filter for the touch,

int raw = 0;
unsigned long total = 0;
int samples = 0;
int average = 0;
uint8_t last_amount = 0;
struct {
    uint8_t start;
    uint8_t amount;
    uint8_t flags;
    uint8_t cksum;
} rx;

struct {
    uint8_t start = 0xAA;
    uint16_t batt;
    uint16_t rx_count;
    uint16_t err_count;
    uint8_t touch;
    uint8_t flags;
    uint8_t cksum;
} tx;

char rx_buf[sizeof(rx)];
char tx_buf[sizeof(tx)];

enum flags {
  FLAG_CHARGE        = 0b00000001,
  FLAG_SERVO_ENABLE  = 0b00000010,
};


Servo servo;
byte CRC8(char *data, byte len);
uint16_t read_batt_mv();

unsigned long mon_count = 0;
unsigned long touch_count = 0;
int touch_val = 0;
bool servo_enable = false;

void setup()
{
  //turn on xbee
  pinMode(XBEE_SLEEP, OUTPUT);
  digitalWrite(XBEE_SLEEP, LOW);

  servo.attach(SERVO);
  pinMode(SERVO_ENABLE, OUTPUT);
  digitalWrite(SERVO_ENABLE, HIGH);
  delay(10);
  servo.write(SERVO_MAX); // move to pen up
  delay(200);
  digitalWrite(SERVO_ENABLE, LOW);

  pinMode(BATT_DIVIDER, OUTPUT);
  digitalWrite(BATT_DIVIDER, LOW);

  Serial.begin(57600);

  pinMode(LED_PEN,OUTPUT);
  pinMode(LED_STATUS,OUTPUT);

  digitalWrite(LED_PEN,HIGH);
  digitalWrite(LED_STATUS,HIGH);

  pinMode(CHARGE, INPUT);
  digitalWrite(CHARGE, HIGH);

  pinMode(BUTTON, INPUT);
  digitalWrite(BUTTON, HIGH);


  tone(BEEP, 5000, 200);
  delay(200);

  tone(BEEP, 3000, 200);
}

uint16_t read_batt_mv()
{
    /* 
    R1 = 10k, R2 = 4.7k
    mv per ADC count = 3300 / 1024
    */
    digitalWrite(BATT_DIVIDER, HIGH);
    delay(2);
    return 4.737 * analogRead(BATT_SENSE);
    digitalWrite(BATT_DIVIDER, LOW);
}
void loop()
{
    // periodically update battery and print stats
    if(millis() > mon_count + MON_INTERVAL)
    {
        mon_count = millis();
        tx.batt = read_batt_mv();

        //charging flag
        /*
        Shutdown Hi-Z 
        No Battery Present Hi-Z 
        Preconditioning L 
        Constant-Current Fast Charge L
        Constant Voltage L
        Charge Complete – Standby H
        */
        if(digitalRead(CHARGE) == LOW) // charging
        {
            digitalWrite(LED_PEN, LOW);
            tx.flags |= FLAG_CHARGE;
        }
        else
        {
            tx.flags &= ~ FLAG_CHARGE;
            digitalWrite(LED_PEN, HIGH);
        }

        if(servo_enable)
            tx.flags |= FLAG_SERVO_ENABLE;
        else
            tx.flags &= ~ FLAG_SERVO_ENABLE;
    }

    if(Serial.available() >= sizeof(rx))
    {
        uint8_t start = Serial.peek();

        if(start != 0xAA)
        {
            // chuck the 1st byte
            Serial.read();
            tx.err_count ++;
            return;
        }
        
        digitalWrite(LED_STATUS,HIGH);
        Serial.readBytes(rx_buf, sizeof(rx));
        tx.rx_count ++;

        //copy buffer to structure
        memcpy(&rx, &rx_buf, sizeof(rx));
        //calculate cksum is ok
        if(rx.cksum != CRC8(rx_buf,sizeof(rx)-1))
        {
            //ignore broken packet
            //Serial.println("err: ck");
            tx.err_count ++;
        }
        else
        {
            //turn on or off servo
            if(rx.flags & FLAG_SERVO_ENABLE)
            {
                servo_enable = true;
                digitalWrite(SERVO_ENABLE, HIGH);
            }
            else
            {
                servo_enable = false;
                digitalWrite(SERVO_ENABLE, LOW);
            }

            //update the servo
            if(rx.amount <= SERVO_MAX && rx.amount >= SERVO_MIN)
                servo.write(rx.amount);
        }
        //send data back
        memcpy(&tx_buf, &tx, sizeof(tx));
        tx.cksum = CRC8(tx_buf,sizeof(tx)-1);

        memcpy(&tx_buf, &tx, sizeof(tx));
        Serial.write(tx_buf, sizeof(tx));

        digitalWrite(LED_STATUS,LOW);
    }
}

//crc from Dallas Semi
byte CRC8(char *data, byte len) 
{
    byte crc = 0x00;
    while (len--)
    {
        byte extract = *data++;
        for (byte tempI = 8; tempI; tempI--) 
        {
            byte sum = (crc ^ extract) & 0x01;
            crc >>= 1;
            if(sum) 
            {
                crc ^= 0x8C;
            }
            extract >>= 1;
        }
    }
    return crc;
}

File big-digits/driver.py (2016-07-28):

"""
title: big 7 segment driver
author: matt venn, 2014
license: GPL attribution share alike
"""
import time

#undefine for testing with GPIO lib
raspi = False
bbb = True

#define which segments are on/off for each digit
#last element is for the point
letters = {
 '0' : [ 1,1,1,1,1,1,0,0 ], # 0
 '1' : [ 0,1,1,0,0,0,0,0 ], # 1
 '2' : [ 1,1,0,1,1,0,1,0 ], # 2
 '3' : [ 1,1,1,1,0,0,1,0 ], # 3
 '4' : [ 0,1,1,0,0,1,1,0 ], # 4
 '5' : [ 1,0,1,1,0,1,1,0 ], # 5
 '6' : [ 0,0,1,1,1,1,1,0 ], # 6
 '7' : [ 1,1,1,0,0,0,0,0 ], # 7
 '8' : [ 1,1,1,1,1,1,1,0 ], # 8
 '9' : [ 1,1,1,0,0,1,1,0 ], # 9
 ' ' : [ 0,0,0,0,0,0,0,0 ], 
 '.' : [ 0,0,0,0,0,0,0,1 ], 
 'P' : [ 1,1,0,0,1,1,1,1 ], 
}

if raspi:
    import RPi.GPIO as GPIO
    GPIO.setwarnings(False)
    GPIO.setmode(GPIO.BOARD)

    #pin defs
    not_oe = 8 #output enable
    le = 10 #latch
    clk = 12 #clock
    sdo = 16 #data out

elif bbb:
    import Adafruit_BBIO.GPIO as GPIO
    from bbb_pwm import PWM

    not_oe = "P9_42" #output enable pwm
    le = "P9_28" #latch
    clk = "P9_41" #clock
    sdo = "P9_30" #data out

if raspi or bbb:
    GPIO.setup(not_oe, GPIO.OUT)
    GPIO.setup(le, GPIO.OUT)
    GPIO.setup(clk, GPIO.OUT)
    GPIO.setup(sdo, GPIO.OUT)

    #turn off leds
    GPIO.output(not_oe, True)
    #turn off latch
    GPIO.output(le,False)
    #clock starts low
    GPIO.output(clk,False)

class driver:
    BLANK = 10
    def __init__(self, verbose=False):
        #verbose output
        self.verbose = verbose

        freq = 200 #hz
        if raspi:
            self.pwm = GPIO.PWM(not_oe, freq)
            #lights off to start with
            self.pwm.start(100) #duty cycle
        if bbb:
            self.pwm = PWM()
            self.pwm.set_pwm(0)

    #sends a string representation of a float, deals with floating points
    def update(self,number):
        point = False
        
        #send least significant digit first
        for char in reversed(number):
            if char == '.':
                point = True
                continue
            self.send_digit(char,point)
            point = False

        #latch the outputs
        if raspi or bbb:
            GPIO.output(le,True)
            GPIO.output(le,False)
        

    #send a char, with optional point
    def send_digit(self,char,point=False):
        #set the point bit
        if point:
            letters[char][7] = 1
        else:
            letters[char][7] = 0

        if self.verbose:
            print("sending %s%s = %s" % (
                char,
                '.' if point else '',
                ','.join(str(x) for x in letters[char]))
                )

        #8 clock pulses
        if raspi or bbb:
            for i in range(8):
                GPIO.output(clk,False)
                #data
                if letters[char][7-i]:
                    GPIO.output(sdo,True)
                else:
                    GPIO.output(sdo,False)

                GPIO.output(clk,True)

    #turn off leds
    def turn_off(self):
        if raspi or bbb:
            self.set_pwm(0)

    #turn on leds
    def turn_on(self):
        if raspi or bbb:
            self.set_pwm(100)


    def set_pwm(self,pwm):
        if raspi:
            self.pwm.ChangeDutyCycle(100-pwm)
        elif bbb:
            self.pwm.set_pwm(100-pwm)

    def fade(self,start,end,length):
        if start > end:
           step = -1
        else:
            step = 1
        for i in range(start,end + step,step):
            time.sleep(float(length) / abs(start-end))
            self.set_pwm(i)

    def cleanup(self):
        self.set_pwm(0)
        self.turn_off()
        GPIO.cleanup()
        #cleanup


#run a test sequence
if __name__ == '__main__':
    driver = driver()
    #driver.set_pwm(100)
    driver.turn_on()
    print("running test sequence")
    point = False
    try:
        while True:
            for i in range(9):
                string = "%d" % (i)
                print("sending %s" % string)
                driver.fade(0,100,0.05)
                driver.update(string)
                time.sleep(1)
                driver.fade(100,0,0.05)
    except KeyboardInterrupt:
        driver.cleanup()

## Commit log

2016-04-10 work around broken adafruit library
    [test_interrupt.py]
2016-05-13 screwthread testing
2016-05-13 test fixture is square
    [plot.py, screwthread-uniformity.ino, test.py]
2016-05-14 fix bug in program that makes bad step amounts
    [screwthread-uniformity.ino, test.py]
2016-05-18 preliminary schematics
    [charger_pcb.sch, reciever_pcb.sch]
2016-05-19 servo test
2016-05-19 new reciever sch
    [reciever_pcb.sch]
2016-05-19 1st reciever pcb
    [reciever_pcb.brd, reciever_pcb.sch]
2016-05-20 emitter 1st pcb
    [charger_pcb.brd, charger_pcb.sch]
2016-05-20 better dir struct, and some tweaks to pcbs
    [charger_pcb.brd, charger_pcb.sch, reciever_pcb.brd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]
2016-05-24 checkpoints revised with Matt, new footprints
    [charger_pcb.brd, charger_pcb.sch, charger_pcb_bom.csv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]
2016-05-25 last touches befor OSHP
    [reciever_pcb.brd]
2016-05-25 1mm dyneema test
2016-05-31 full BOMs
    [charger_pcb_bom.csv, reciever_pcb_bom.csv]
2016-05-31 full BOMs again...
    [reciever_pcb_bom.csv]
2016-06-10 slide homing
2016-06-13 mostly laid out
    [bbbbbb.sch, gondola.sch, ledssch.sch]
2016-06-13 first pass pcb layout
    [bbbbbb.kicad_pcb, bbbbbb.sch, gondola.sch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]
2016-06-14 footprints mostly done
    [bbbbbb.kicad_pcb, bbbbbb.sch, gondola.sch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]
2016-06-14 gondola charge
    [bbbbbb.kicad_pcb, bbbbbb.sch, gondola.sch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]
2016-06-16 stepper choices
2016-06-16 silkscreen & values
    [bbbbbb.kicad_pcb, bbbbbb.sch, gondola.sch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]
2016-06-20 gondola pcb
    [gondola.sch]
2016-06-22 gondola pcb to fab
    [gondola.kicad_pcb]
2016-06-22 fixed solder mask over touch ring
    [gondola.kicad_pcb]
2016-06-24 oshpark fab
    [bbbbbb.kicad_pcb, bbbbbb.sch, gondola.sch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]
2016-06-29 working ok at 25ms, hal ok
    [xbee.hal]
2016-06-29 fixed cksum, better pin names
    [xbee.hal]
2016-06-30 stepper choice
2016-06-30 moved to machinekit config repo
    [xbee.hal]
2016-07-02 fix debug print
2016-07-09 got pwm working by using /sys
2016-07-09 get rid of swserial as it causes servo jitter
    [gondola.ino]
2016-07-09 delay necessary to get adc flushed
2016-07-12 missing r values
    [gondola.sch]
2016-07-12 fixed cap val
    [gondola.sch]
2016-07-15 fixed stupid serial comms error, added charge flag
    [gondola.ino]
2016-08-01 track error
2016-09-08 battery usage pic
2016-09-09 turn off servo when charging
2016-09-09 code for enabling servo
2016-10-04 notes on charger chip
2016-10-19 sleep on xbee pin, dont boot till voltage is >3500mv
2016-10-20 found random power down issue
2016-10-24 gondola charger addon board
    [gondola_charger.kicad_pcb, gondola_charger.sch]
2016-10-25 return a reply even in the event of a broken cksum
    [gondola.ino]
2016-10-27 mcp73832 and extra hole
    [gondola_charger.kicad_pcb, gondola_charger.sch]
2016-10-27 final version
    [gondola_charger.kicad_pcb]
2016-11-02 low power test
2016-11-07 magnet idea
2016-11-17 firmware for November fix
    [gondola.ino]
